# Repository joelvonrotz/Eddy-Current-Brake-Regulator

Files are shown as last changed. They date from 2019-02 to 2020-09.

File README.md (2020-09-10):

# Eddy Current Brake Regulator
This Repository is for the storage of all files and references used in the documentation.
Additionally the mechanical plans, KiCAD files, used for the PCB, and the Latex Project is included here.

# Geregelte Wirbelstrombremse
Dieses *Repository* beinhaltet alle verwendeten Informationen bezüglich der Maturaarbeit *Geregelte Wirbelstrombremse*. Alle mechanischen Pläne, Leiterplattendaten und das Latex-Projekt selber wird hier abgespeichert.

:warning: This is my very first Latex-project, so expect a lot of workarounds :warning:

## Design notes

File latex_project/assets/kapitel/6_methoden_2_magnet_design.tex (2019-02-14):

\subsection{Magnet Design}\label{cap:methoden_magnet_design}
Die Form des Magneten war abhängig von mehreren Faktoren. Einerseits musste der Magnet anhand der elektronischen Vorgaben angepasst werden, anderseits limitierte das Rad des Fitnesstrainers den Platz für den Magnet.

\input{assets/images/manget_uc.tex}

Im Normalfall besteht eine Magnetbremse aus einer Metall-Scheibe, welche eine gute Leitfähigkeit besitzt, und einem C-förmiger Magnet, welcher in der Öffnung die Scheibe platziert wird. Wenn der Platz ungenügend ist, kann eine zusätzliche eisenhaltige Scheibe hinzugefügt werden und der C-förmige Magnet durch einen U-förmigen Magnet ersetzt werden, wobei dieser nicht unten platziert wird, sondern seitlich der Scheibe (Siehe Abbildung \ref{fig:magnet_uc}). Dieser Aufbau erlaubt es, die zu bremsende Scheibe von der Seite an zu bremsen, anstatt von unten. Der Nachteil ist der Energieverlust zwischen den Luftspalten, welcher sich fast verdoppelt. 
\newpara
Da das Rad des Fitnesstrainers zu breit ist und daher den Platz für ein C-förmiger Magnet zu eng ist, wurde für ein U-förmiges Magnet entschieden. Im Anhang können die Pläne für die Eisen- und Aluminium-Platte und für das Magnet gefunden werden. Diese Pläne wurden in der CAD-Software \textit{Fusion 360} von Autodesk erstellt.
\newpara
Der Magnet wurde anhand der von W.R. Smythe geschriebenen Arbeit \textit{Eddy Current on a Rotating Disk}(\cite{current_on_a_rotating_disk}) erstellt. Diese Formel wurde von Empfehlung einer externen Person verwendet, da diese Person mit dieser Formel gearbeitet hatte. Von Smythes Arbeit wurde die Formel 22 für die Berechnung des Magneten verwendet (Siehe Formel \ref{equ:smythe_orignal}).

\begin{equation}
  \label{equ:smythe_orignal}
  M = \frac{\omega_{MAX}\cdot b \cdot \gamma \cdot \Phi^{2}\cdot c^{2}}{2\cdot\pi\cdot a^{2}}\cdot(1-\frac{A^{2}\cdot a^{2}}{(A^{2}-c^{2})^{2}})
\end{equation}
\begin{gather}
\shortintertext{\textbf{Begriffe:}}
\begin{tabularx}{0.9\textwidth}{ll}
  $\omega_{MAX}$	& maximale Kreisfrequenz\\
  $\Phi$          & Magnetischer Fluss \\
  $\gamma$	      & Elektronische Leitfähigkeit der Spule am Magnet\\
  $a$             & Radius der Magnetpoolfläche welche auf die Scheibe gerichtet ist\\
  $c$             & Radius der Magnetposition von dem Mittelpunkt der Scheibe ausgerichtet\\
  $b$             & Dicke der Scheibe\\
  $A$             & Radius der Scheibe (nur für diese Formel)\\
  $M$             & Drehmoment
\end{tabularx}\nonumber
\end{gather}

Die maximale Kreisfrequenz wurde anhand einer Drehzahlmessung mit dem Messgerät \textit{Braun gmbh MOVIPORT C118} und mit einem menschlichen Versuchstier ermittelt. Durch starkes Antreten der Pedale mit dem Messgerät konnte die maximale Drehzahl ermittelt werden. Wird die Formel der Kreisfrequenz (Siehe Formel \ref{equ:rotation_max}) in die Formel (Formel \ref{equ:smythe_orignal}) eingesetzt, kann die Kreisfrequenz durch die Drehzahl ersetzt werden (Siehe Formel \ref{equ:smythe_rotation_included}).

\begin{equation}
  \label{equ:rotation_max}
  \omega_{MAX}=2\cdot\pi n_{MAX}
\end{equation}
\begin{gather}
\shortintertext{\textbf{Begriffe:}}
\begin{tabularx}{0.9\textwidth}{ll}
  $n_{MAX}$	& maximale Drehzahl
\end{tabularx}\nonumber
\end{gather}
(\cite[S.193]{kuchling2014taschenbuch})
\newpara
\begin{equation}
  \label{equ:smythe_rotation_included}
  M = \frac{\cancel{2\cdot\pi}\cdot n_{MAX}\cdot b \cdot \gamma \cdot \Phi^{2}\cdot c^{2}}{\cancel{2\cdot\pi}\cdot a^{2}}\cdot(1-\frac{A^{2}\cdot a^{2}}{(A^{2}-c^{2})^{2}})
\end{equation}

Die gesamte Form des Magneten wird anhand des magnetischen Flusses berechnet, da in der Formel des Flusses (Siehe Formel \ref{equ:magnetischer_fluss}) der magnetische Widerstand, welche abhängig von der Form des Magneten ist, und die magnetische Durchflutung (Siehe Formel \ref{equ:magnetische_durchflutung}), welche von der Stromstärke und der Anzahl Wicklungswindungen am Magnet abhängig ist, eingesetzt wird. Der magnetische Widerstand besteht aus mehreren Teilwiderstände, welche allen Teilen des Magneten und der Luftspalte entsprechen (Siehe Formel \ref{equ:magnetischer_widerstand} \& \ref{equ:magnetischer_serie_widerstand}).

\begin{equation}
  \label{equ:magnetischer_fluss}
  \Phi = \frac{\Theta}{R_m}
\end{equation}
\begin{gather}
\shortintertext{\textbf{Begriffe:}}
\begin{tabularx}{0.9\textwidth}{ll}
  $\Theta$	 &  magnetische Durchflutung\\
  $\Phi$	 &  magnetischer Fluss\\
  $Rm$ &  magnetischer Widerstand
\end{tabularx}\nonumber
\end{gather}
(\cite{schulmaterial_magnetismus})
\newpage
\begin{equation}
  \label{equ:magnetische_durchflutung}
  \Theta = N\cdot I
\end{equation}
\begin{gather}
\shortintertext{\textbf{Begriffe:}}
\begin{tabularx}{0.9\textwidth}{ll}
  $N$	 &  Anzahl Windungen der Wicklung\\
  $I$	 &  elektrische Stromstärke
\end{tabularx}\nonumber
\end{gather}
(\cite{schulmaterial_magnetismus})
\newpara
\begin{figure}[ht]
  \begin{center}
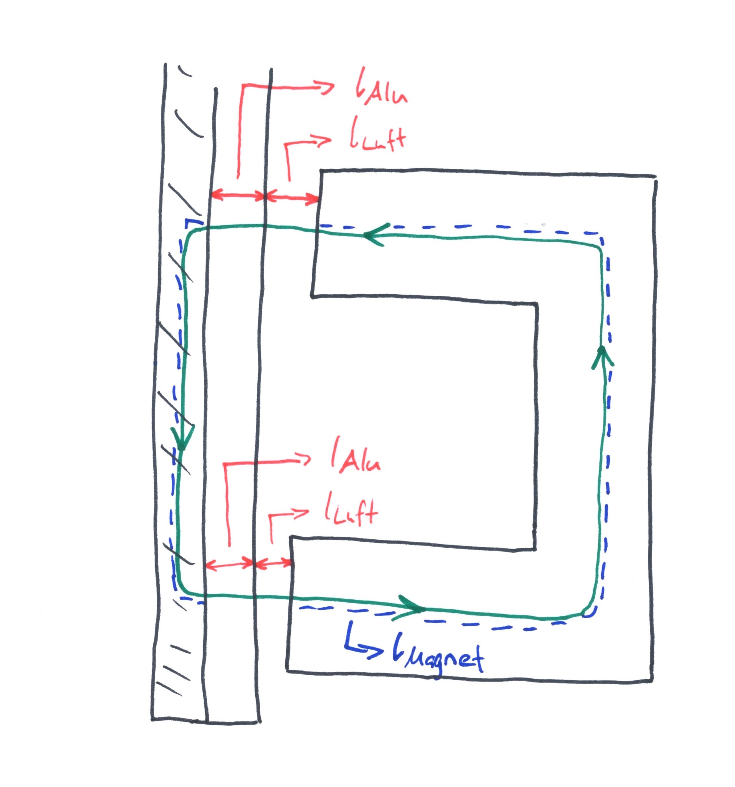
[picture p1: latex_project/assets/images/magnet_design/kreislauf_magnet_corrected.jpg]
    
  \end{center}
  \vspace{-3ex}
  \caption{Magnetkreis bei Magnet und Scheibe}
  \label{fig:magnet_kreisllaenge}
\end{figure}
\newpage
\begin{equation}
  \label{equ:magnetischer_widerstand}
  R_m=\frac{l}{\mu_0 \cdot \mu_r \cdot A}
\end{equation}
\begin{gather}
\shortintertext{\textbf{Begriffe:}}
\begin{tabularx}{0.9\textwidth}{ll}
  $\mu_0$  & magnetische Feldkonstante = 1.257E-06	Vs/Am\\
  $\mu_r$  & Permeabilitätszahl (1 $\equalhat$ Vakuum, $\gg$ 1 $\equalhat$ ferromagnetisch)\\
  $A$	  & Querschnittsfläche des Elements\\
  $R_m$  & Magnetischer Widerstand\\
  $l$	  & Länge des magnetischen Kreises (Siehe Abbildung \ref{fig:magnet_kreisllaenge})
\end{tabularx}\nonumber
\end{gather}
(\cite{schulmaterial_magnetismus})
\newpara
Mit dem magnetischen Widerstand (Siehe Formel \ref{equ:magnetischer_widerstand}) wird in Kombination mit der magnetischen Durchflutung die Magnetstärke (magnetischer Fluss) berechnet. Wird ein starkes Magnet benötigt, wird je nach Möglichkeit entweder die Durchflutung angepasst oder der magnetische Widerstand durch Verkleinerung des Luftspaltes.
\newpara
Der Luftspalt reduziert die magnetische Flussdichte, was den Magneten davon abhält, gesättigt zu werden. Ist ein Magnet gesättigt, wird überflüssige Energie in Wärme umgewandelt. Der Effekt des Luftspalts ist wegen dem magnetischen Widerstand des Vakuums. Die Permeabilitätszahl vom Vakuum ist gleich $1$ und entspricht daher der magnetischen Feldkonstante ($\mu_0 \cdot 1 = \mu_0$). Bereits bei einer Querschnittsfläche von $1m^2$ und einem Luftspalt von $1m$ beträgt der magnetische Widerstand $\frac{1m}{1\cdot 1.257\cdot 10^{-6}\frac{N}{A^2}\cdot 1m^2}=795'798\frac{A}{Vs}$. Bei einem Eisenstück mit einer Permeabilitätszahl von $10'000$ würde der magnetische Widerstand $\frac{1m}{10'000\cdot 1.257\cdot 10^{-6}\frac{N}{A^2}\cdot 1m^2}=79,58\frac{A}{Vs}$ entsprechen, 10'000 kleiner als der Widerstand des Luftspalts. Der Nachteil des Luftspalts ist die Schwächung der Magnetstärke, was zu einer schwächeren Bremse führt.
\newpara
Bei der Wirbelstrombremse ist es wichtig, ein starkes Magnet zu haben. Das bedeutet, dass einen kleinen magnetischen Widerstand benötigt wird.
\newpara

\begin{equation}
  \label{equ:magnetischer_serie_widerstand}
  R_{mGES}=R_{m Luft}+R_{m Alu}+R_{m Magnet}
\end{equation}
\begin{gather}
\shortintertext{\textbf{Begriffe:}}
\begin{tabularx}{0.9\textwidth}{ll}
  $R_{mGES}$  & magnetische Gesamtwiderstand\\
  $R_{m Luft}$  & mag. Widerstand der Luftspalte\\
  $R_{m Alu}$  & mag. Widerstand der Aluminiumscheibe\\
  $R_{m Magnet}$  & mag. Widerstand des Magneten\\
\end{tabularx}\nonumber
\end{gather}
(\cite{schulmaterial_magnetismus})
\newpara
Der gesamte magnetische Widerstand ist abhängig von der Dicke der Aluminiumscheibe, der Dicke des Luftspalts und die magnetischen Kreislänge des Magneten (Siehe Formel \ref{equ:magnetischer_serie_widerstand}). Abbildung \ref{fig:magnet_design_u_magnet_luftspalt} zeigt den Nachteil eines seitlichen Aufbaus im Vergleich eines C-förmigen Magneten (Siehe Abbildung \ref{fig:magnet_design_c_magnet_luftspalt} folgende Seite).  
\begin{figure}[ht]
\begin{center}
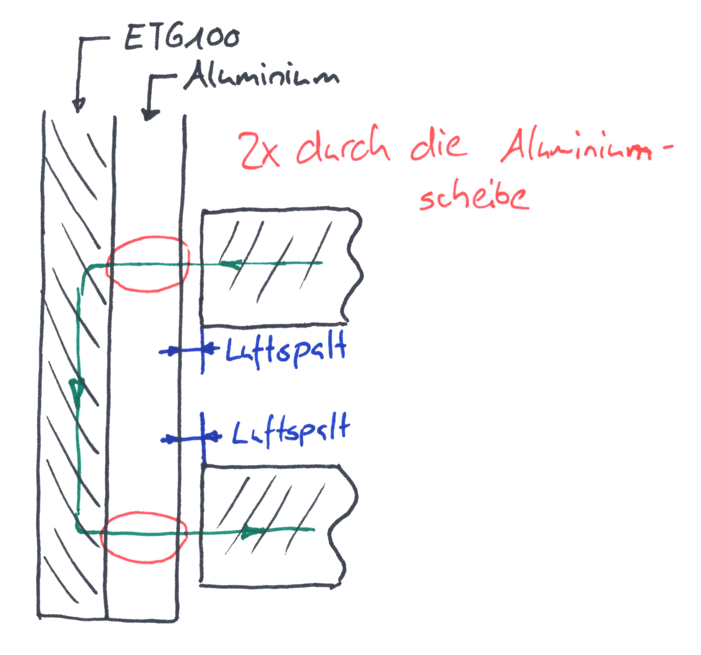
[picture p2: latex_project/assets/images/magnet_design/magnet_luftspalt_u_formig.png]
  
\end{center}
\vspace{-3ex}
\caption{Luftspalt eines U-förmigen Magnets}
\label{fig:magnet_design_u_magnet_luftspalt}
\end{figure}

\begin{figure}[ht]
\begin{center}
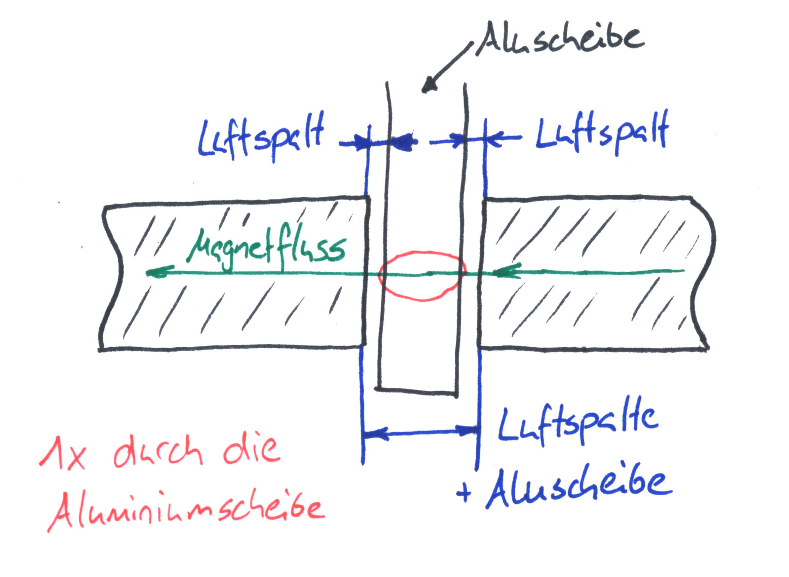
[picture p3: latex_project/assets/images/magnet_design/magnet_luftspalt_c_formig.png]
  
\end{center}
\vspace{-3ex}
\caption{Luftspalt eines C-förmigen Magnets}
\label{fig:magnet_design_c_magnet_luftspalt}
\end{figure}

Der Luftspalt kann gleich behalten werden, aber die Kreislänge der Aluminiumscheibe verdoppelt sich, was zu einem doppelten Aluminiumwiderstand führt (Siehe Formel \ref{equ:magnetischer_widerstand_alueinfluss}). Da Aluminium dem Vakuum sehr nahe kommt, hat dies einen grossen Einfluss auf die Magnetstärke.

\begin{equation}
  \label{equ:magnetischer_widerstand_alueinfluss}
  R_m=R_{m Luft}+2 \cdot R_{m Alu}+R_{m Magnet}
\end{equation}
\newpara
Das Drehmoment M in der Formel \ref{equ:smythe_rotation_included} wird durch das Trägheitsdrehmoment ersetzt (Siehe Formel \ref{equ:Drehmoment_tragheit}), da die Bremse abhängig von der zu bremsenden Scheibe ist.

\begin{equation}
  \label{equ:Drehmoment_tragheit}
  M=J\cdot\alpha
\end{equation}
\begin{gather}
\shortintertext{\textbf{Begriffe:}}
\begin{tabularx}{0.9\textwidth}{ll}
  $M$  & Drehmoment\\
  $J$  & Trägheitmoment\\
  $\alpha$ & Winkelbeschleunigung
\end{tabularx}\nonumber
\end{gather}
(\cite[S.127]{kuchling2014taschenbuch})
\newpara
Das Trägheitsmoment gibt die Beeinflussung der Masse von der Scheibe auf die Bremse an (Siehe Formel \ref{equ:tragheitsmoment}). Die Winkelgeschwindigkeit gibt die zeitliche Änderung der Winkelgeschwindigkeit innerhalb von zwei Zeitpunkten an (Siehe Formel \ref{equ:winkelbeschleunigung}).

\begin{equation}
  \label{equ:tragheitsmoment}
  J=m\cdot r^2
\end{equation}
\begin{gather}
\shortintertext{\textbf{Begriffe:}}
\begin{tabularx}{0.9\textwidth}{ll}
  $J$  & Trägheitsmoment\\
  $m$  & Masse der Scheibe\\
  $r$ & Radius der Scheibe
\end{tabularx}\nonumber
\end{gather}
(\cite[S.131]{kuchling2014taschenbuch})
\newpara
\begin{equation}
  \label{equ:winkelbeschleunigung}
  \alpha=\frac{\Delta\omega}{\Delta t}
\end{equation}
\begin{gather}
\shortintertext{\textbf{Begriffe:}}
\begin{tabularx}{0.9\textwidth}{ll}
  $\Delta\omega$  & Kreisfrequenzänderung während der Zeit $\Delta t$\\
  $\Delta t$  & Zeit während zwei Zeitpunkten \\
\end{tabularx}\nonumber
\end{gather}
(\cite[S.88]{kuchling2014taschenbuch})
\newpara
Die Kreisfrequenzänderung und die Zeitdifferenz sind bei der Berechnung Annahmen (der Wert wurde von der Gruppe vorgegeben).
\newpara
Nun wurde die Formel \ref{equ:tragheitsmoment} und die Formel \ref{equ:winkelbeschleunigung} in die Formel \ref{equ:Drehmoment_tragheit} eingesetzt, was zu einer neuen Formel führt (Formel \ref{equ:tragheitsmoment_kombiniert}). Die Dimensionierung basiert nun auf dem \textit{Trial-and-Error} Prinzip. Mit unterschiedlichen Dimensionen wird die Formel (Formel \ref{equ:smythe_rotation_included}) verwendet, bis anhand eines nutzbaren Resultats die Dimensionen des Magnets ermittelt werden konnte. 
\newpara
\begin{equation}
  \label{equ:tragheitsmoment_kombiniert}
  M=\frac{m\cdot r^2\cdot\Delta\omega}{\Delta t}
\end{equation}
\newpara
Folgende Angaben wurde für den aktuellen Magneten verwendet:
\newpara
\begin{tabularx}{0.9\textwidth}{lll}
$\mu_R$	       & $3000$		&Annahme, da kein definitiver Wert existiert\\
$N$	           & $300$		\\
$I$	           & $2 A$\\
$l_{LUFT}$	   & $8 mm$\\
$l_{Fe}$ 	     & $1.05 mm$\\
$a$	           & $0.015 m$\\
$b$	           & $0.003 m$\\
$c$	           & $0.1 m$\\
$A$	           & $0.15 m$\\
$n_{MAX}$	     & $25 s^{-1}$	\\
$\Delta\omega$ & $5 s^{-1}$	  &	Gewünschte Abbremsung innerhalb $\Delta t$\\
$\Delta t$	   & $5 s$        &	Zeit für $\Delta\omega$\\
$\alpha$	     & $1 rad\cdot s^{-2}$&	Winkelbeschleunigung von $\Delta t$ und $\Delta\omega$\\
$m_{RAD}$	     & $5.747 kg$	  & Gewicht des Rades\\
$\Phi$	       & $76.43\cdot 10^{-6} Vs$\\
$\gamma$	     & $6.21\cdot 10^{6} Sm^{-1}$
\end{tabularx}\nonumber
\newpara
daraus ergab sich:
\newpara
\begin{tabularx}{0.9\textwidth}{lll}
  $M_{MAG}$	   & $0.0186 Nm$		& Drehmoment der Bremse\\
  $M_{MASS}$   & $0.00647 Nm$		& Trägheit des Rades\\
\end{tabularx}\nonumber
\newpara
Anhand dieser Resultate sollte der Magnet stärker sein als die Massenträgheit der Scheibe. Was sich aber bei den Messungen herausstellte, stimmte dieser Wert nicht überein mit den Resultaten. Die Begründung, warum diese Resultate nicht stimmen, wird im Kapitel \ref{cap:diskussion} erläutert.
\newpara
\begin{tcolorbox}
  Hier geschahen der erste und zweite Fehler: 1) das Trägheitsdrehmoment (Formel \ref{equ:Drehmoment_tragheit}) wurde nicht mit der Formel von Smythe (Formel \ref{equ:smythe_rotation_included}) kombiniert, sondern die beiden Drehmomente wurden verglichen, was zu einem eher ungenauen Magneten führte. 
  \newpara
  2) Der zweite Fehler ist die Fehlberechnung der Dimensionen. Anstatt die Formel (Formel \ref{equ:smythe_rotation_included}) korrekt zu verwenden wurde stattdessen mit der folgenden Formel (Formel \ref{equ:wrong_calculation}) gerechnet. Die Winkelfrequenz-Formel wurde nicht korrekt eingesetzt und gekürzt, was zu einem falschen Resultat führte.

  \begin{equation}
    \label{equ:wrong_calculation}
    M=\frac{n_{MAX}\cdot b\cdot\gamma\cdot\Phi^2\cdot c^2}{2\cdot\pi\cdot a^2}\cdot(1-\frac{A^{2}\cdot a^{2}}{(A^{2}-c^{2})^{2}})
  \end{equation}
  \newpara
  Im Kapitel \ref{cap:diskussion} wird die vollständige Formel aufgeführt.
\end{tcolorbox}

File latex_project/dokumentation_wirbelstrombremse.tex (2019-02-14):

%!TEX TS-program = xelatex
%!TEX encoding = UTF-8 Unicode

\documentclass[12pt]{article} % A4 paper size, default 11pt font size and oneside for equal margins
\usepackage[bottom=2.54cm, left=2.54cm, right=2.54cm, top=2.54cm]{geometry}
\usepackage[english,german]{babel}
\usepackage[toc,numberedsection]{glossaries}
\usepackage[style=alphabetic, citestyle=authoryear,date=iso, urldate=iso]{biblatex}
\usepackage{titlesec}
\usepackage[x11names]{xcolor}
\usepackage{tcolorbox}
\usepackage{scalerel,stackengine,amsmath}
\usepackage{textcomp}
\usepackage[T1]{fontenc}
\usepackage{tikz}
\usepackage{pgfplots}
\usepackage{siunitx}
\usepackage{mathtools}
\usepackage{cancel}
\usepackage{qrcode}
\usepackage{tabularx}
\PassOptionsToPackage{hyphens}{url}
\usepackage{hyperref}
\usepackage{dirtytalk}
\usepackage{float}

\batchmode

\renewcommand*{\nameyeardelim}{\addcomma\space}
\usetikzlibrary{positioning,fit,calc,arrows.meta,arrows}
\usepgfplotslibrary{units}
\newcommand\equalhat{\mathrel{\stackon[1.5pt]{=}{\stretchto{%
    \scalerel*[\widthof{=}]{\wedge}{\rule{1ex}{3ex}}}{0.5ex}}}}

\tikzset{
  labelbox/.style={draw,thick,text width=2.5cm,minimum height=1cm,align=center},
  round/.style={circle,draw,thin, minimum size=5mm},
  emptynode/.style={draw=none},
  arrow_right/.style={-{Latex[length=2mm]}},
  spot/.style={draw,shape=circle,fill=black,inner sep=1.5pt, minimum size = 0.5mm}
}

\pgfplotsset{
  compat=1.16,
  axis_regulator_style/.style={
    width=8.8cm,
    axis x line=center,
    axis y line=left,
    xlabel style={right = 0cm and 0.1cm},
    ylabel style={above left},
    legend cell align={left}
  },
  axis_results_style/.style={
    width=8.8cm,
    axis x line=bottom,
    axis y line=left,
    legend cell align={left}
  },
  line_black/.style={
    color=black!70,
    line width= 1pt
  },
  line_blue/.style={
    color=blue!70,
    line width= 1pt
  },
  line_red/.style={
    color=red!70,
    line width= 1pt
  }
}

\newcommand{\newpara}
{
  \vskip 0.5cm
}
\raggedbottom

\newlength\tindent
\setlength{\tindent}{\parindent}
\setlength{\parindent}{0pt}
\renewcommand{\indent}{\hspace*{\tindent}}

% \usepackage{newtxtext}
% \usepackage{amsmath}
% \usepackage[mathrm=sym]{unicode-math}
% \setmathfont{Fira Math}

%----------------------------------------------------------------------------------------
%	TITLE PAGE
%----------------------------------------------------------------------------------------

\makeglossaries
\loadglsentries{assets/glossar.tex}
\bibliography{literature_and_stuff}

\begin{document} 
\input{assets/titlepage.tex}
\tableofcontents
\vskip 2cm

\input{assets/kapitel/1_vorwort.tex}

\input{assets/kapitel/2_abstract.tex}
\newpage

\input{assets/kapitel/3_einleitung.tex}
\newpage
\section{Einlesung}\label{cap:einlesung}
\input{assets/kapitel/4_einlesung_1_magnetismus.tex}
\input{assets/kapitel/4_einlesung_2_physik.tex}
\input{assets/kapitel/4_einlesung_3_regler.tex}
\newpage
\section{Material}\label{cap:material}
\input{assets/kapitel/5_material_1_mechanik.tex}
\input{assets/kapitel/5_material_2_magnet.tex}
\input{assets/kapitel/5_material_3_elektronik.tex}

\section{Methoden}\label{cap:methoden}
\input{assets/kapitel/6_methoden_1_planung.tex}
\newpage
\input{assets/kapitel/6_methoden_2_magnet_design.tex}
\input{assets/kapitel/6_methoden_3_leiterplatten.tex}
\newpage
\input{assets/kapitel/6_methoden_4_aufbau.tex}
\input{assets/kapitel/6_methoden_5_drehzahl.tex}
\input{assets/kapitel/6_methoden_6_magnetbremsung.tex}
\newpage
\input{assets/kapitel/6_methoden_7_radanpassung.tex}
\newpage
\input{assets/kapitel/6_methoden_8_datenauswertung.tex}
\newpage
\input{assets/kapitel/6_methoden_9_magnet_control.tex}
\newpage
\section{Ergebnisse}\label{cap:ergebnisse}
\input{assets/kapitel/7_ergebnisse_1_drehzahlmessung.tex}
\newpage
\input{assets/kapitel/7_ergebnisse_2_magnetabbremsung.tex}
\newpage
\section{Diskussionen} \label{cap:diskussion}
\input{assets/kapitel/8_diskussion_1_drehzahlmessung.tex}
\input{assets/kapitel/8_diskussion_2_magnetabbremsung.tex}
\newpage
\input{assets/kapitel/8_diskussion_3_nichterreichung.tex}
\input{assets/kapitel/8_diskussion_4_schlussfolgerung.tex}

\section{Schlusswort} \label{cap:schlusswort}
\input{assets/kapitel/9_schlusswort.tex}
\newpage

\input{assets/kapitel/10_abbildungsverzeichnis.tex}
\newpage

\input{assets/kapitel/11_glossar.tex}
\newpage

\input{assets/kapitel/12_literaturverzeichnis.tex}
\newpage

\section{Anhang}
\input{assets/kapitel/13_anhang.tex}

% https://www.latextemplates.com/template/formal-book-title-page - template

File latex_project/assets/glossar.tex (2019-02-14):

\newglossaryentry{glos:frequenz}
{
  name={Frequenz},
  description={Anzahl der Schwingungen im Verhältnis zu der dafür benötigten Zeit}
}

\newglossaryentry{glos:kinetische_energie}
{
  name={Kinetische Energie},
  description={Das ist die Energie, welche in einem sich bewegenden Körper gespeichert ist. Wird auch als Energie der Bewegung bezeichnet.}
}

\newglossaryentry{glos:induktion}
{
  name={Induktion},
  description={Zeitliche Änderung des magnetischen Flusses, die durch die Bewegung eines Leiters im Magnetfeld Erzielt wird. Im Leiter entsteht eine elektrische Spannung.}
}

\newglossaryentry{glos:wirbelstrom}
{
  name={Wirbelstrom},
  description={Bewegt sich ein elektrisch leitender Körper in einem Magnetfeld, wird in dem Teil, der sich gerade durch das Magnetfeld bewegt eine Spannung induziert. Das führt zu einer Spannungsdifferenz im Körper. Diese wird mit Wirbelströmen ausgeglichen.}
}

\newglossaryentry{glos:magnetfeld}
{
  name={Magnetfeld},
  description={Raum, in dem ein Magnet Kraft ausübt.}
}

\newglossaryentry{glos:ferromagnetisch}
{
  name={Ferromagnetisch},
  description={Stoffe, die von Magneten angezogen werden.}
}

\newglossaryentry{glos:elektronen}
{
  name={Elektronen},
  description={Negativ geladenes Teilchen n der Atomhülle.}
}

\newglossaryentry{glos:magnetischer_fluss}
{
  name={Magnetischer Fluss},
  description={Die Gesamtzahl aller Magnetischen Feldlinien in einem Magneten.}
}

\newglossaryentry{glos:c_schiene}
{
  name={C-Schiene},
  description={C-förmiges Metallstück, welches für Befestigungen von Elektronik dient.}
}

\newglossaryentry{glos:etg_100}
{
  name={ETG-100},
  description={Metall mit Eiseninhalt.}
}

\newglossaryentry{glos:mcu}
{
  name={Mikrocontroller},
  description={Ein Baustein, welcher aus Halbleitern besteht. Können meistens in kleinen simplen Geräten aufgefunden werden, wie zum Beispiel in einer Fernbedienung.}
}

\newglossaryentry{glos:fpu}
{
  name={FPU},
  description={Steht für Floating Point Unit und wird für Berechnungen von Kommazahlen verwendet.}
}

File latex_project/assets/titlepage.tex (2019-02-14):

\begin{titlepage} % Suppresses headers and footers on the title page

	\centering % Centre everything on the title page
  \vspace*{10mm}
  {\LARGE GEREGELTE} % Title
  \newpara
  {\LARGE WIRBELSTROMBREMSE}
  \vskip 10mm
  \input{assets/images/aufbau.tex}

  {Verfasser}

	{\Large Joel von Rotz \\ Stefan Ruckli \\ \vspace{0.25\baselineskip} Filip Estermann} % Editor list
  \vskip 1cm
    Betreuungslehrperson

    {\large Antonio Russo}
  \vskip 1cm
	\textit{BBZB Luzern} % Editor affiliation
  Februar 2019 % Publication year
	{IDPA-Nr. 1094} % Publisher

\end{titlepage}

%----------------------------------------------------------------------------------------
\author{Joel von Rotz\\Stefan Ruckli\\Filip Estermann}
\date{Februar 2019}

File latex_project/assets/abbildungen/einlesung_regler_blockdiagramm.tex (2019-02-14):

\begin{figure}[ht]
  \begin{center}
    \begin{tikzpicture}
      \node[emptynode]    (soll)                                {};
      \node[round]        (diff)        [right=1cm of soll]     {};
      \node[labelbox]     (regl)        [right=1cm of diff]     {Regler};
      \node[labelbox]     (akto)        [right=1cm of regl]     {Aktor};
      \node[labelbox]     (sens)        [below=1cm of akto]     {Sensor};
      \node[labelbox]     (stre)        [right=1cm of akto]     {Regelstrecke};
      \node[emptynode]    (gone)        [right=2cm of stre]     {};
      \node[emptynode]    (erro)        [above=1cm of stre]     {z};
      \node[emptynode]    (minus_diff)  [below right = -1mm and -1mm of diff] {$-$};
      %\node[emptynode]    (plus_diff)   [above left  = -1mm and -1mm of diff] {$+$};
      \node[spot]         (midl)        [right=1cm of stre]     {};

      \draw [arrow_right] (soll)      -- node[above left = 0cm and 1mm]   {$w$} (diff);
      \draw [arrow_right] (diff)      -- node[above left = 0cm and -1mm]  {$e$} (regl);
      \draw [arrow_right] (regl)      -- node[above]                      {$m$} (akto);
      \draw [arrow_right] (akto)      -- node[above]                      {$y$} (stre);
      \draw [-]           (stre)      -- node[above left]                 {$x$} (gone);
      \draw [arrow_right] (midl.center) |-                                      (sens.east);
      \draw [arrow_right] (sens.west) -| node[above left  = 1cm and 0cm]  {$r$} (diff.south);
      \draw [arrow_right] (erro)      --                                            (stre);
    \end{tikzpicture}
  \end{center}
  \vspace{-3ex}
  \caption{Regler Blockdiagramm}
  \label{fig:regulator_block}
\end{figure}

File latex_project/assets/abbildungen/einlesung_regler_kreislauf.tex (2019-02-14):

\begin{figure}[ht]
  \begin{center}
    \begin{tikzpicture}
      \node[labelbox]     (mess)                                          {Messen};
      \node[labelbox]     (verg)  [below right= 3cm and 0.5cm of mess]    {Vergleichen};
      \node[labelbox]     (stel)  [below left = 3cm and 0.5cm of mess]    {Stellen};

      \node[emptynode]    (nod0)  [below right= 0.2cm and 0.2cm of mess]  {};
      \node[emptynode]    (nod1)  [above      = 0.2cm of verg]            {};
      \node[emptynode]    (nod2)  [      left = 0.2cm of verg]            {};
      \node[emptynode]    (nod3)  [      right= 0.2cm of stel]            {};
      \node[emptynode]    (nod4)  [above      = 0.2cm of stel]            {};
      \node[emptynode]    (nod5)  [below left = 0.2cm and 0.2cm of mess]  {};

      \draw [arrow_right] (nod0) -- (nod1);
      \draw [arrow_right] (nod2) -- (nod3);
      \draw [arrow_right] (nod4) -- (nod5);

    \end{tikzpicture}
  \end{center}
  \vspace{-3ex}
  \caption{Regler Blockdiagramm}
  \label{fig:regulator_circulation}
\end{figure}

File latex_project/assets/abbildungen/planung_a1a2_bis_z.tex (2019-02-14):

\begin{figure}[ht]
    \begin{center}
      \begin{tikzpicture}
        \node[emptynode]     (a1)                                        {$A_1$};
        \node[emptynode]     (a2)   [below= 2cm of a1]                     {$A_2$};
        \node[emptynode]     (z)    [below right= 0.9cm and 5cm of a1]                     {Z};
        \node[emptynode]     (e1)   [right= 2cm of a1]                                  {};
        \node[emptynode]     (e2)   [right= 2cm of a2]                     {};
        \node[emptynode]     (e3)   [below right= 1cm and 3cm of a1]                     {};
  
        \draw [-] (a1) -- (e1.center);
        \draw [-] (a2) -- (e2.center);
        \draw [-] (e2.center) -- (e3.center);
        \draw [-] (e1.center) -- (e3.center);
        \draw [arrow_right] (e3.center) -- (z);
      \end{tikzpicture}
    \end{center}
    \vspace{-3ex}
    \caption{Parallele Vorgehensweise}
    \label{fig:planung_a1a2_bis_z}
  \end{figure}

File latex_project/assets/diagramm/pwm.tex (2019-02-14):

\begin{figure}[h]
  \begin{center}
    \begin{tikzpicture}
      \begin{axis}[
        axis_regulator_style,
               %title         = P-Regler mit konstanter Abweichung,
               ylabel         = {Spannung},
               y unit         = {V},
        ylabel near ticks, 
        yticklabel pos        = left,
        minor      grid style = {dashed,gray},
                   ymax       = 2,
                   ymin       = 0,
                   xmax       = 20,
                   xlabel     = {t},
                   xticklabels    = {,,},
        legend     style      = {draw=none}
      ]
      
        \addplot[line_red] table[x=time,y=value,col sep=comma,mark=none]{assets/diagramm/pwm.csv};
        \addlegendentry{PWM-Verlauf}
      \end{axis}
      \draw[<->](0.37,2) -- node[above]{Pause} (2.88,2);
      \draw[<->](2.90,2) -- node[right =0.3cm]{Impuls} (3.60,2);
      \draw[-](0.37,3) -- (0.37,4);
      \draw[-](3.62,3) -- (3.62,4);
      \draw[<->](0.37,3.8) -- node[above]{Periode} (3.62,3.8);
    \end{tikzpicture}
  \end{center}
  \vspace{-3ex}
  
  \caption{PWM Darstellung}
  \label{fig:plot_pwm}
\end{figure}

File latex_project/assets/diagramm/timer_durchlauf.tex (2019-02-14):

\begin{figure}[h]
  \begin{center}
    \begin{tikzpicture}
      \begin{axis}[
        axis_regulator_style,
               %title         = P-Regler mit konstanter Abweichung,
               yticklabels    = {,,},
               xticklabels    = {,,},
        ylabel near ticks, 
        yticklabel pos        = left,
        minor      grid style = {dashed,gray},
                   ymax       = 10,
                   ymin       = 0,
                   xmax       = 20,
                   xlabel     = {t},
        legend     style      = {draw=none}
      ]
        \addplot[line_blue] table[x=time2,y=value2,col sep=comma,mark=none]{assets/diagramm/timer_durchlauf.csv};       
        \addlegendentry{Magnetschalter}
      
        \addplot[line_red] table[x=time,y=value,col sep=comma,mark=none]{assets/diagramm/timer_durchlauf.csv};    
        \addlegendentry{Timer}
      \end{axis}
      \draw[<->](0,2.7) -- node[above]{Zeit für eine Umdrehung} (5.78,2.7);
      \draw[-,black!70,thick](5.78,0.6) -- (5.78,3.6);
    \end{tikzpicture}
  \end{center}
  \vspace{-3ex}
  
  \caption{Eine Radumdrehung}
  \label{fig:plot_timer_magnetschalter_impuls}
\end{figure}

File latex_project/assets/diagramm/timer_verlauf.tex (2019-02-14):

\begin{figure}[h]
  \begin{center}
    \begin{tikzpicture}
      \begin{axis}[
        axis_regulator_style,
               %title         = P-Regler mit konstanter Abweichung,
               ylabel         = {Zählerstand},
               xticklabels    = {,,},
        ylabel near ticks, 
        yticklabel pos        = left,
        minor      grid style = {dashed,gray},
                   ymax       = 23,
                   ymin       = 0,
                   xmax       = 20,
                   xlabel     = {t},
        legend     style      = {draw=none}
      ]
      
        \addplot[line_red] table[x=time,y=value,col sep=comma,mark=none]{assets/diagramm/timer_verlauf.csv}; 
        \addlegendentry{Timer}
      \end{axis}
      \draw[<->](2.90,2.8) -- node[above =0.3cm,font = {\fontsize{8 pt}{16 pt}\selectfont}]{Zeit für ein Inkrement} (3.25,2.8);
      \draw[-](3.25,2.5) -- (3.25,3);
      \draw[-](2.90,2.2) -- (2.90,3);
      \draw[-](5.77,4) -- (5.77,5);
      \draw[<->](0,4.8) -- node[above,font = {\fontsize{8 pt}{16 pt}\selectfont}]{Zeit für ein Interval} (5.77,4.8);
    \end{tikzpicture}
  \end{center}
  \vspace{-3ex}
  
  \caption{Intervall Durchgang des Timers}
  \label{fig:plot_timer_verlauf}
\end{figure}

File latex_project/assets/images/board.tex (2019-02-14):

\begin{figure}[ht]
    \begin{center}
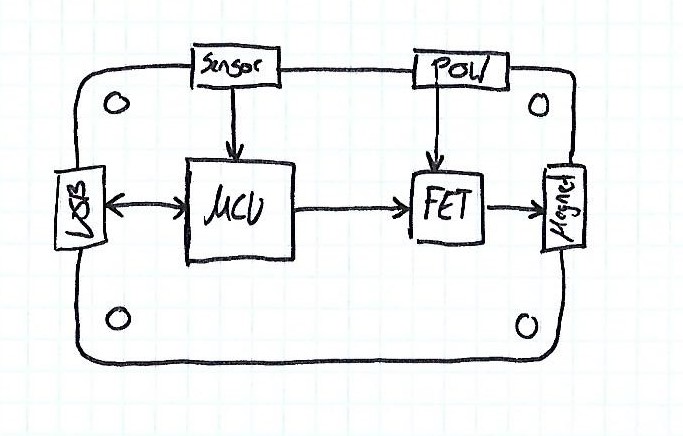
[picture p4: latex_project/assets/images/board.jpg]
      
    \end{center}
    \vspace{-3ex}
    \caption{Skizze des Leiterplattenlayouts}
    \label{fig:board}
  \end{figure}

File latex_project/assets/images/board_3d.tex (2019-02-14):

\begin{figure}[ht]
    \begin{center}
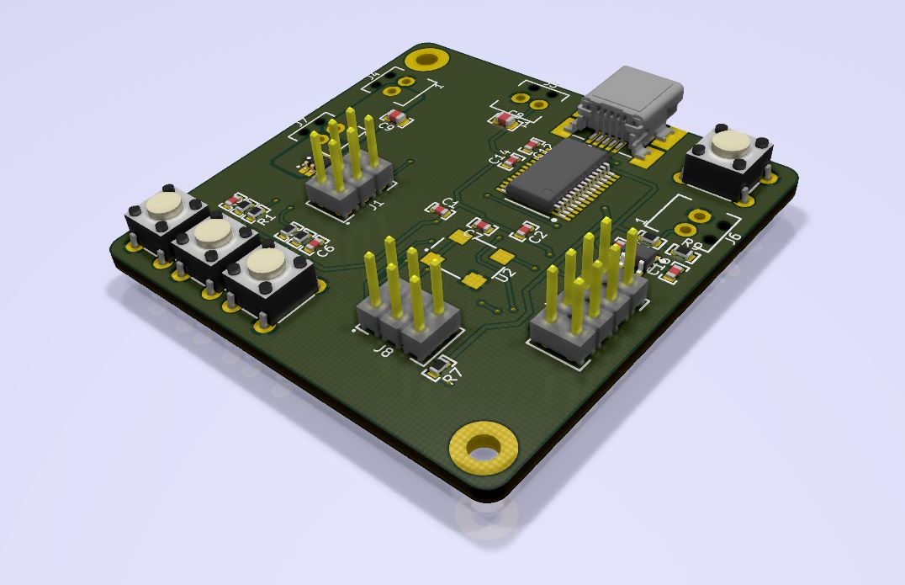
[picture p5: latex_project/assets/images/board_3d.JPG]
      
    \end{center}
    \vspace{-3ex}
    \caption{3D Model der fertigen Leiterplatte}
    \label{fig:3d_board}
  \end{figure}

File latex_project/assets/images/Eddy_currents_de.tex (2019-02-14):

\begin{figure}[ht]
    \begin{center}
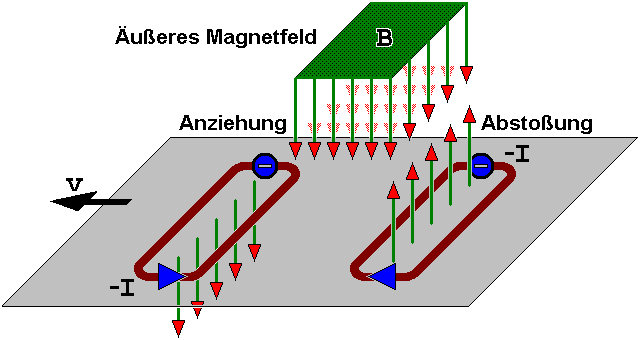
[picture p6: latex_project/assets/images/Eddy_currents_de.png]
      
    \end{center}
    \vspace{-3ex}
    \caption[Wirbelstrombremse auf einer Metallplatte]{\centering{Wirbelstrombremse auf einer Metallplatte. Heruntergeladen von \texttt{https://de.wikipedia.org/wiki/Wirbelstrombremse}}}
    \label{fig:eddy_current}
  \end{figure}

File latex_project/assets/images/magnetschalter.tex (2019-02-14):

\begin{figure}[ht]
    \begin{center}
      
    \end{center}
    \vspace{-3ex}
    \caption{Bild des Magnetschalter}
    \label{fig:magnetschalter}
  \end{figure}

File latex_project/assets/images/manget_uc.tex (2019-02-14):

\begin{figure}[ht]
    \begin{center}
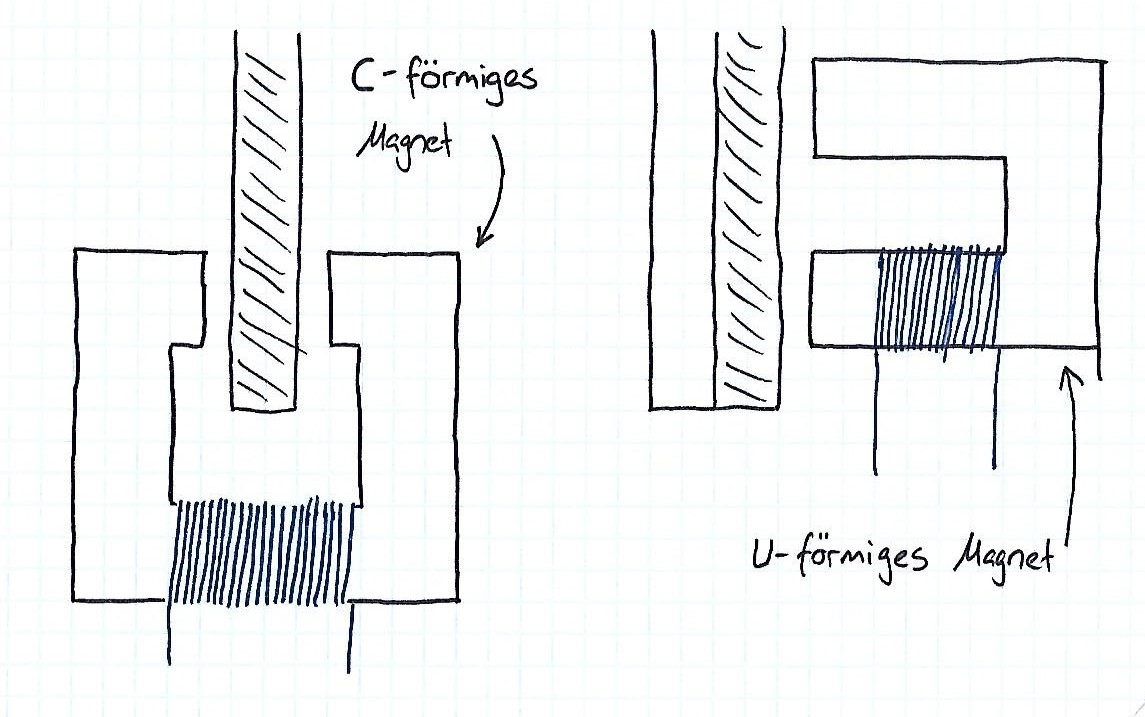
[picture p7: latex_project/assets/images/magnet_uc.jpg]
      
    \end{center}
    \vspace{-3ex}
    \caption{U-förmiges und C-Förmiges Magnet}
    \label{fig:magnet_uc}
  \end{figure}

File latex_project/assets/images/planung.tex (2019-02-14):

\begin{figure}[ht]
    \begin{center}
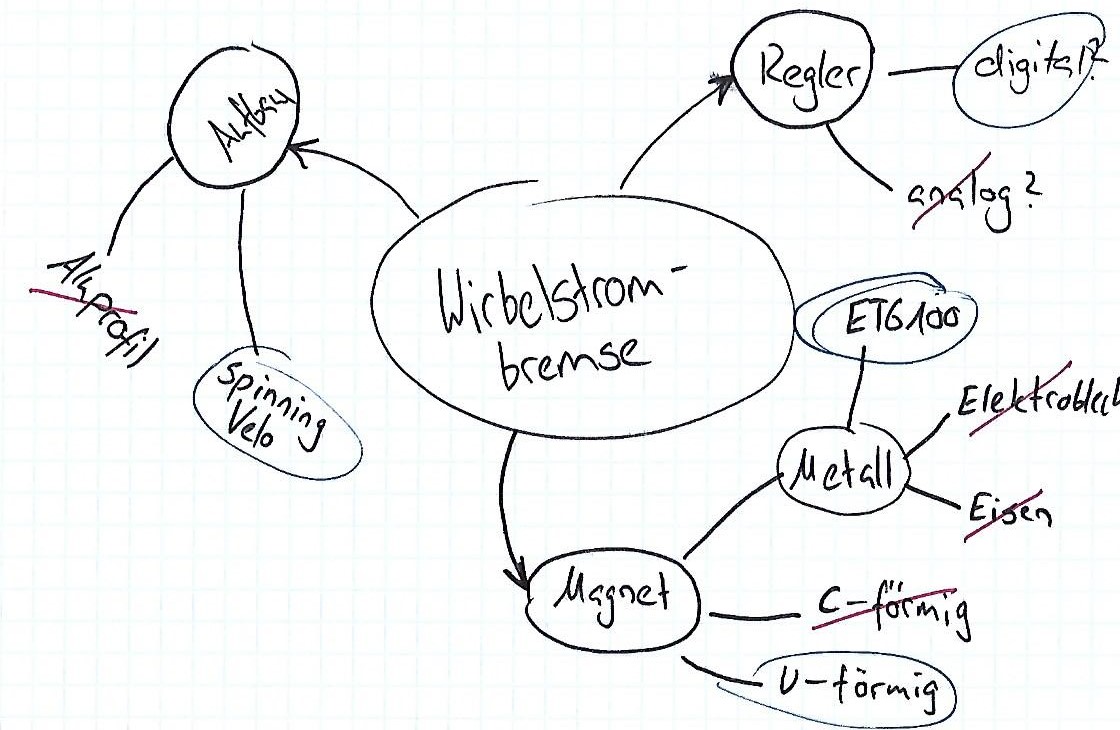
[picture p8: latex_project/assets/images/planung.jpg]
      
    \end{center}
    \vspace{-3ex}
    \caption{Mindmap}
    \label{fig:mindmap}
  \end{figure}

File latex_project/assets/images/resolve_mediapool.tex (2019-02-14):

\begin{figure}[ht]
    \begin{center}
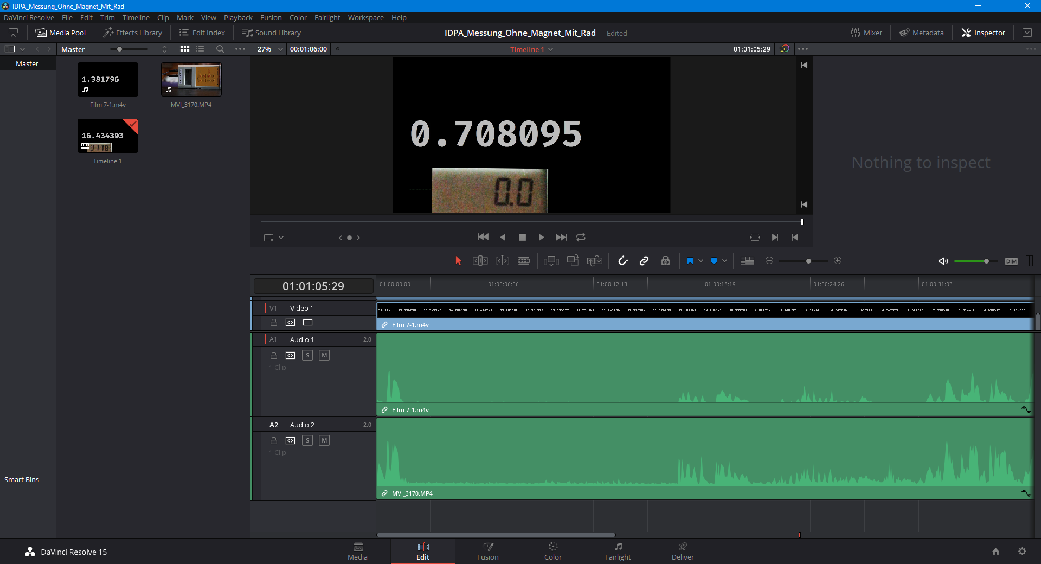
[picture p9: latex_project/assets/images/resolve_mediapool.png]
      
    \end{center}
    \vspace{-3ex}
    \caption{Ausschnitt aus Davinci Resolve}
    \label{fig:resolve_mediapool}
  \end{figure}

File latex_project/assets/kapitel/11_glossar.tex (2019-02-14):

\setglossarystyle{altlisthypergroup}
\printglossary
\glsaddallunused

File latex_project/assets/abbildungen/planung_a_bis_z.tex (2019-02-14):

\begin{figure}[ht]
    \begin{center}
      \begin{tikzpicture}
        \node[emptynode]     (a)                                           {A};
        \node[emptynode]     (z)   [right= 5cm of a]                     {Z};

        \draw [arrow_right] (a) -- (z);

      \end{tikzpicture}
    \end{center}
    \vspace{-3ex}
    \caption{Einfache Vorgehensweise}
    \label{fig:planung_a_bis_z}
  \end{figure}

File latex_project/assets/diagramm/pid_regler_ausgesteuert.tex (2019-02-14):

\begin{figure}[h]
  \begin{center}
    \begin{tikzpicture}
      \begin{axis}[
        axis_regulator_style,
               %title      = P-Regler mit konstanter Abweichung,
               ylabel     = {},
        ylabel near ticks, 
        yticklabel pos        = left,
        minor      grid style = {dashed,gray},
                   xmax       = 110,
                   xlabel     = {t},
                   xticklabels    = {,,},
        legend     style      = {draw=none}
      ]
        \addplot[line_blue] table[x=time,y=pid,col sep=comma,mark=none]{assets/diagramm/pid_regler_ausgesteuert.csv}; 
        \addlegendentry{P + I + D}
      
        \addplot[line_red] table[x=time,y=e,col sep=comma,mark=none]{assets/diagramm/pid_regler_ausgesteuert.csv};        
        \addlegendentry{Abweichung}
        
      \end{axis}
    \end{tikzpicture}
  \end{center}
  \vspace{-3ex}
  
  \caption{PID-Regler mit Schwingungen}
  \label{fig:plot_pid_regulator_out_of_control}
\end{figure}

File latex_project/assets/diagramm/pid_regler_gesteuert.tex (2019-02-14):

\begin{figure}[h]
  \begin{center}
    \begin{tikzpicture}
      \begin{axis}[
        axis_regulator_style,
               %title      = P-Regler mit konstanter Abweichung,
               ylabel     = {},
        ylabel near ticks, 
        yticklabel pos        = left,
        minor      grid style = {dashed,gray},
                   ymax       = 1.5,
                   ymin       = -0.5,
                   xmax       = 110,
                   xlabel     = {t},
                   xticklabels    = {,,},
        legend     style      = {draw=none}
      ]
      
        \addplot[line_red] table[x=time,y=e,col sep=comma,mark=none]{assets/diagramm/pid_regler_gesteuert.csv};    
        \addlegendentry{Abweichung}
        
        \addplot[line_blue] table[x=time,y=pid,col sep=comma,mark=none]{assets/diagramm/pid_regler_gesteuert.csv}; 
        \addlegendentry{P + I + D}
      \end{axis}
    \end{tikzpicture}
  \end{center}
  \vspace{-3ex}
  
  \caption{PID-Regler mit Rückkopplung}
  \label{fig:plot_pid_regulator_controlled}
\end{figure}

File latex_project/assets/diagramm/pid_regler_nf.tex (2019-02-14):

\begin{figure}[h]
  \begin{center}
    \begin{tikzpicture}
      \begin{axis}[
        axis_regulator_style,
               %title         = P-Regler mit konstanter Abweichung,
               ylabel         = {},
        ylabel near ticks, 
        yticklabel pos        = left,
        minor      grid style = {dashed,gray},
                   ymax       = 4,
                   ymin       = -0.5,
                   xmax       = 110,
                   xlabel     = {t},
                   xticklabels    = {,,},
        legend     style      = {draw=none}
      ]
      
        \addplot[line_red] table[x= time,y= e,col sep=comma,mark=none]{assets/diagramm/pi_regler_nf.csv};        
        \addlegendentry{Abweichung}
      
        \addplot[line_blue] table[x= time,y=pid,col sep=comma,mark=none]{assets/diagramm/pid_regler_nf.csv}; 
        \addlegendentry{P + I + D}
      \end{axis}
    \end{tikzpicture}
  \end{center}
  \vspace{-3ex}
  
  \caption{PID-Regler mit konstanter Abweichung}
  \label{fig:plot_pid_regulator_no_feedback}
\end{figure}

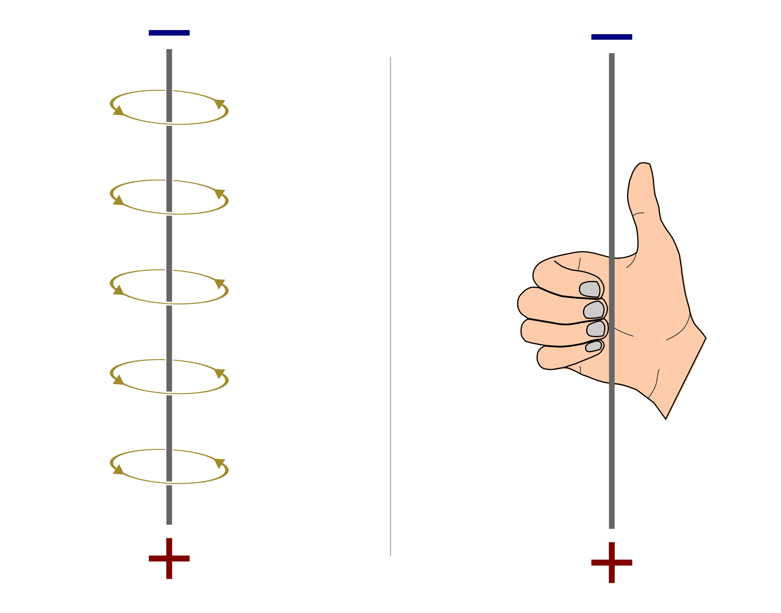
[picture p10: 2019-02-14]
latex_project/assets/images/magnetismus/magnetfeld-leiter-rechte-hand-regel.png

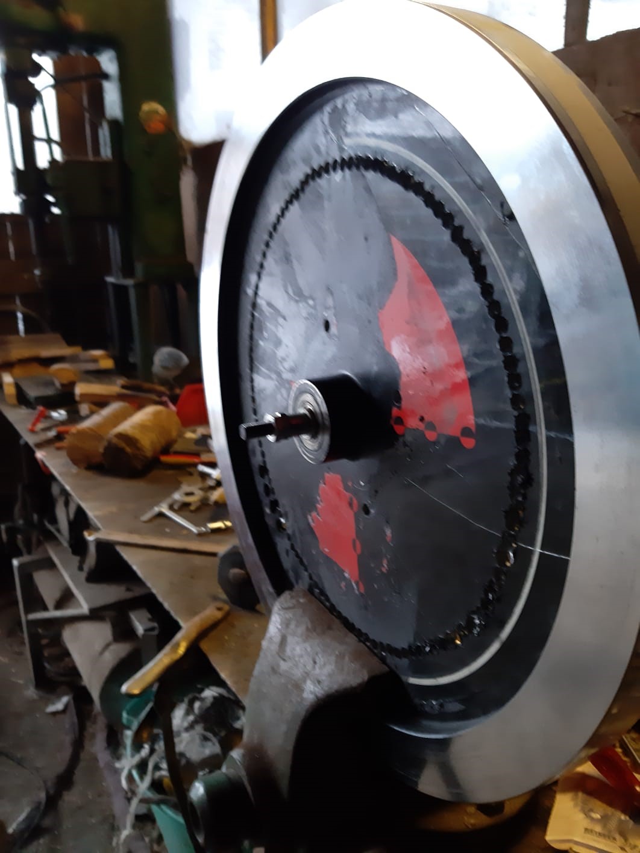
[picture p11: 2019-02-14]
latex_project/assets/images/rad.png

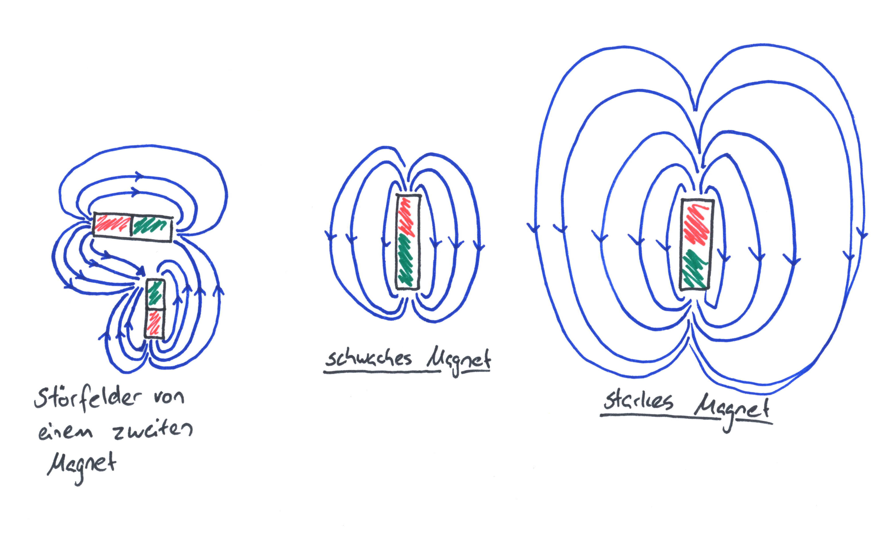
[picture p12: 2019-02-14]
latex_project/assets/images/magnetismus/beeinflussungen_magnet.jpg

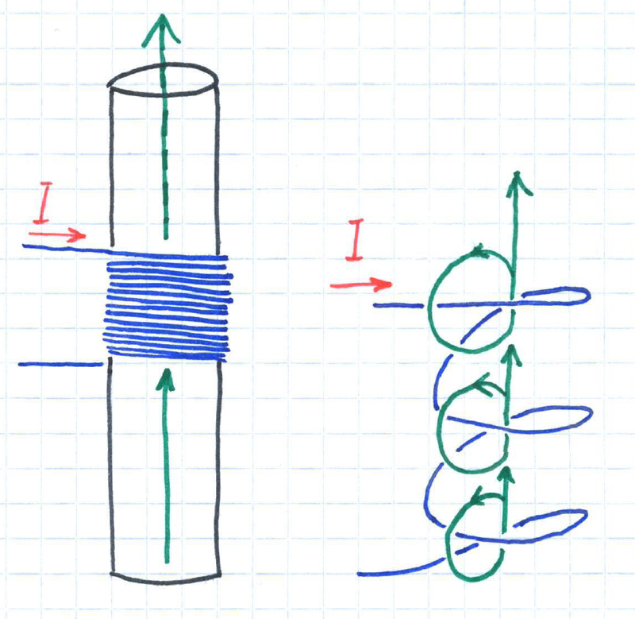
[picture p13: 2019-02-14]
latex_project/assets/images/magnetismus/flussrichtung.PNG

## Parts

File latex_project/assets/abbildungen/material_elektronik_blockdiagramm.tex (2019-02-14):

\begin{figure}[ht]
    \begin{center}
      \begin{tikzpicture}
        \node[labelbox]     (mcu)                                           {MCU};
        \node[labelbox]     (fet)  [right= 2cm of mcu]    {MOSFET};
        \node[labelbox]     (usb)   [above = 2cm of mcu]    {USB};
        \node[emptynode]    (sens)  [left=2cm of mcu]  {Sensor};
  
        \draw [arrow_right] (sens) -- (mcu);
        \draw [arrow_right] (mcu) -- (fet);
        \draw [arrow_right] (mcu) -- (usb);
  
      \end{tikzpicture}
    \end{center}
    \vspace{-3ex}
    \caption{Schaltung Blockdiagramm}
    \label{fig:electronic_block}
  \end{figure}

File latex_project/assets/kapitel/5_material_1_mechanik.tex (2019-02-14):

\subsection{Mechanik}
Die Hauptbedingung an das mechanische Gestell war, dass es ein drehbares Rad aufweisen soll, welches leicht in Bewegung gebracht werden kann. Ausserdem muss sich das Rad auch über eine längere Zeit selbst drehen können. Diese Bedingungen führten dazu, ein Spinning Wheel zu beziehen. Solch ein Spinning Wheel wird als Fitnessgerät verwendet. 
\newpara
Bei der Bremsscheibe wurde eine Aluminium-Scheibe verbaut. Dieses Metall wurde verwendet, da dies einen guten elektrischen Leitwert aufweist und somit auch gute Bremseigenschaften mit sich bringt. Ausserdem besitzt Aluminium als Leichtmetall ein relativ geringes spezifisches Gewicht.
\newpara
Hinter der Aluminium Scheibe befindet sich eine zweite, dickere Scheibe aus Automatenstahl. Hier wurde ETG 100 Automatenstahl verbaut, weil sich dieser leicht magnetisieren lässt und das Magetfeld vergleichsweise gut leiten kann.
\newpara
Als Haltegestell für den Elektromagneten wurden zwei parallel geführte C-Schienen verwendet, damit der Abstand zwischen dem Elektromagneten und der Bremsscheibe variiert werden kann. Ein ausserdem positiver Aspekt der C-Schienen ist, dass diese aus Aluminium bestehen und somit den Elektromagneten, ferromagnetisch von dem Eisengestell trennen. Somit kann eine höhere Wirkungskraft aus dem Magneten erzielt werden. Damit der Elektromagnet an seiner rechten Stelle bleibt, wurde dieser mit Schnellverlegern auf die Schiene geschraubt. Diese Schnellverleger ermöglichen ein rasches bewegen – und fixieren von dem Magnet. 
\newpara
Damit diese zwei C-Schienen sich in einer stabilen und korrekten Lage befinden, wurde ein Gestell gefertigt und die Schienen montiert. Dieses wurde aus dicken Blechplatten konstruiert. Aufgrund einer starken mechanischen Festigkeit wurde jenes Material verbaut. Dieses Eisengestell wurde mit Nieten an das Spinning Wheel gefügt.

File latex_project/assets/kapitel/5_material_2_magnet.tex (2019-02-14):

\subsection{Magnet}
Wichtiger Bestandteil eines Magneten ist das Metall. Das Metall muss ferromagnetisch sein, damit es etwas anziehen kann. Die Magnetisierbarkeit ist abhängig vom Eiseninhalt des Metalls. Je mehr Eisen das Metall hat, desto stärker wird das Magnetfeld bei gleichem Volumen sein (\cite{schulmaterial_magnetismus}). Also war das Ziel der Metall-Wahl, ein Metall herauszusuchen, welches sich für das magnetische Bremsen eignet.
\newpara

\newpara
Für diese Arbeit wurde das Metall \textbf{ETG-100} verwendet. Die Wahl wurde mit Hilfe einer externen Person ausgewählt, weil diese Person sich für das Thema interessierte und bereits selbst Wirbelstrombremsen entworfen hatte.
\newpara
Die Permeabilitätszahl, welche für den Magneten benötigt wird, konnte nur anhand einer Annahme gesetzt werden. Anhand eines Physikbuches wurde der Bereich für ferromagnetische Stoffe 300 bis 10'000 vorgenommen (\cite[S.661]{kuchling2014taschenbuch}). Als Annahme wurde daraus die Permeabilitätszahl 5'000 gesetzt.

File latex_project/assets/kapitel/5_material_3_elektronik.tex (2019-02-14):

\subsection{Elektronik} \label{cap:material_electronics}
Für die richtige Wahl der Komponenten mussten zuerst Voraussetzungen gesetzt werden. Die Voraussetzungen der Elektronik ist das Messen der Geschwindigkeit des Rades, die Regelung der Bremse und eine Möglichkeit die gemessenen Daten auslesen zu können. 

\input{assets/abbildungen/material_elektronik_blockdiagramm.tex}

Der Regler konnte daraus in drei Blöcken aufgeteilt werden: USB, Mikrocontroller und MOSFET. Mit dem USB war das Ziel, Daten auslesen zu können und den Sollwert zu setzen. Der Mikrocontroller würde als Sensor und Gehirn der Elektronik dienen und wäre für das Messen der Geschwindigkeit, die Ansteuerung des Magneten und das Berechnen der Regelung würde der Mikrocontroller zuständig. Der MOSFET dient als Schalter um den Magneten anzusteuern.
\newpara
In den folgenden Unterkapiteln werden die Auswahl und die Begründung der ausgewählten Komponenten aufgeführt.

\subsubsection{Mikrocontroller}
Die wichtigste Komponente ist der Mikrocontroller, welcher einen grossen Anteil an Arbeit übernehmen muss, welche das Messen und das Regeln beinhalten. Zum Messen der Geschwindigkeit und für die Regelung des Magneten werden Timer benötigt. Timer sind in der Elektronik Peripherien, welche mit Events verknüpft werden können. Es ist also möglich einen Event mit einem Timer zu verknüpfen, damit Prozesse, welche einen gleichmässigen Takt benötigen, zuverlässig ausgeführt werden. Der Regler verwendet einen Timer, damit das Integral und das Differenzial mit einer konstanten Abtastrate berechnet werden können. Dies hat den Vorteil, dass die Berechnungen einfacher und genauer berechnet werden können.
\newpara
Ein Interrupt-System dient zur Verknüpfung von Events mit verschiedenen Peripherien. Bei der Bremse wurde ein solches System eingebaut, damit die Geschwindigkeitsmessung genauer berechnet werden kann. Ein Interrupt selbst ist ein Unterbruch im Prozess, welcher von Peripherien ausgelöst werden kann. Bei einem Interrupt wird der aktuelle Prozess gestoppt und ein anderer Prozess wird ausgeführt. Am Ende dieses Prozesses wird wieder mit dem normalen Prozess weitergemacht.
\newpara
Die wichtigsten Kriterien für den Mikrocontroller, aus dem oberen Ausschnitt hergeleitet, sind die Geschwindigkeit des Controllers, Timer Peripherie und ein Interrupt-System. Der Speicherplatz ist ebenfalls wichtig, da das Programm gross werden kann. Zusätzlich hätte ein FPU noch einberechnet werden können, aber dies würde den Controller teurer machen und wird bereits mit der Controllergeschwindigkeit kompensiert. 
\newpara
Aus Familiarität wurde ein Mikrocontroller der Firma Microchip ausgewählt. Neben der Familiarität existiert bereits eine grosse Community, welche Mikrocontroller verwenden und daher auch Dokumentationen von vielen Funktionen existieren. Aus Recherche und eigener Erfahrung konnten zwei Mikrocontroller ausgewählt werden: Atmega328P und Atmega328PB. Beide sind im Aufbau sehr ähnlich, ausser dass der Atmega328PB einige Verbesserungen besitzt.
\newpara
Für das Projekt wurde der \textbf{Atmega328PB} ausgewählt, weil er bessere Timer besitzt, welche länger laufen können, was zu weniger Belastung des Mikrocontrollers führt.
\subsubsection{USB}
Die Aufgabe eines USB-Chips ist es, eine Verbindung zwischen einem Computer und einer Elektronik zu erstellen, damit ein Datenaustausch ausgeführt werden kann. In unserem Fall ist es der Datenaustausch von Geschwindigkeitsmessung.
\newpara
Als USB-Schnittstellen-Chip wurde der \textbf{FT232RL} von FTDI ausgewählt. Dieser wurde ausgewählt, da bereits gute Erfahrungen mit diesem Chip gemacht wurden. Wenn ein anderer Chip ausgewählt würde, müsste man zuerst sich über die elektronischen Verbindungen informieren (wo muss mit was verbunden werden).

\subsubsection{MOSFET}
Ein MOSFET ist ein elektronischer Schalter. Im Vergleich zum normalen mechanischen Schalter, welche von Hand betätigt werden kann, wird der MOSFET via einem elektronischen Signal betätigt.
\newpara
Bei der Auswahl des MOSFETs muss auf die Belastbarkeit und Grösse geachtet werden. Unter Belastbarkeit ist die maximale Zufuhr von elektronischer Energie gemeint. Bei zu grosser Energie kann es sein, dass der MOSFET explodiert und grossen Schaden an der Elektronik anrichtet. Als Grenzwerte wurde die minimale Belastbarkeit für den Magneten auf 2A begrenzt und die Grösse auf Maximum 2 x 2cm begrenzt. Zur Auswahl standen die folgende MOSFETs:
\newpage
\begin{itemize}
    \item CSD18511 von Texas Instruments
    \item Si4436DY von Vishay
    \item CPH6442 von ON-Semiconductor
\end{itemize}

Für das Projekt wurde der \textbf{CPH6442} ausgewählt. Die Begründung ist die Grösse des Bausteins. In einem 2.8mm x 2.9mm Gehäuse kann dieser Chip eine Belastung von maximal 6A aushalten, was genügend für das Magnet ist. Die maximale Spannung beträgt 60V und ist auch für den Magneten geeignet, da der Widerstand der Wicklung klein ist und daher bei 2A eine kleine Spannung erzeugt. Die anderen Bausteine besassen ähnlichen Attributen, scheiterten aber bei der Grösse.

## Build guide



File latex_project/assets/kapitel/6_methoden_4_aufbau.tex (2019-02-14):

\subsection{Aufbau} \label{cap:methoden_aufbau}

Der Aufbau setzt sich aus sich aus folgenden Elementen zusammen: 
\begin{itemize}
\item Elektromagnet		
\item C-Schienen	
\item Aluminumscheibe	
\item ETG-100 Scheibe
\item Gestell für den Elektromagnet
\end{itemize}

Die ETG-100 Scheibe wird als erstes an das Schwungrad montiert. Auf die ETG-100 Platte folgt direkt die Aluminiumscheibe. Diese Armatur wurde starr verschraubt. 
Auf die Stand-Eisenträger des Spinning Wheels wurde das Gestell für den Elektromagneten fixiert. Auf dieses Gestell wurden die zwei C-Schienen angeschgraubt. Auf den C-Schienen wurde der Elektromagnet montiert. Dieser U-förmige Magnet schaut anschliessend mit den Pol-Austritten genau auf die Aluminiumscheibe zu. Die Wicklungen wurden über die Zylinder des Elektromagneten angebracht (Abbildung \ref{fig:gesamtaufbau}).

\begin{figure}[ht]
  \begin{center}
    
  \end{center}
  \vspace{-3ex}
  \caption{Gesamtaufbau}
  \label{fig:gesamtaufbau}
\end{figure}

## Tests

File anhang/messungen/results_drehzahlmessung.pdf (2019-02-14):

index | electronic | mess | mess_converted ratio_el_me | time
1 | 3.987241 | 221.2 | 3.687 | 1.082 | 0.267
2 | 4.093529 | 221.2 | 3.687 | 1.110 | 0.533
3 | 4.228115 | 239.5 | 3.992 | 1.059 | 0.800
4 | 4.374912 | 239.5 | 3.992 | 1.096 | 1.067
5 | 4.477398 | 239.5 | 3.992 | 1.122 | 1.333
6 | 4.524723 | 239.5 | 3.992 | 1.134 | 1.600
7 | 4.638907 | 263.9 | 4.398 | 1.055 | 1.867
8 | 4.771721 | 263.9 | 4.398 | 1.085 | 2.133
9 | 4.901192 | 263.9 | 4.398 | 1.114 | 2.400
10 | 4.968598 | 263.9 | 4.398 | 1.130 | 2.667
11 | 5.20573 | 289.3 | 4.822 | 1.080 | 2.933
12 | 5.257845 | 289.3 | 4.822 | 1.090 | 3.200
13 | 5.377269 | 289.3 | 4.822 | 1.115 | 3.467
14 | 5.531463 | 289.3 | 4.822 | 1.147 | 3.733
15 | 5.660207 | 320.8 | 5.347 | 1.059 | 4.000
16 | 5.775806 | 320.8 | 5.347 | 1.080 | 4.267
17 | 5.909607 | 320.8 | 5.347 | 1.105 | 4.533
18 | 5.998081 | 320.8 | 5.347 | 1.122 | 4.800
19 | 6.12565 | 350.6 | 5.843 | 1.048 | 5.067
20 | 6.216432 | 350.6 | 5.843 | 1.064 | 5.333
21 | 6.349045 | 350.6 | 5.843 | 1.087 | 5.600
22 | 6.533556 | 350.6 | 5.843 | 1.118 | 5.867
23 | 6.693799 | 378.8 | 6.313 | 1.060 | 6.133
24 | 6.903026 | 378.8 | 6.313 | 1.093 | 6.400
25 | 7.00437 | 378.8 | 6.313 | 1.109 | 6.667
26 | 7.181432 | 378.8 | 6.313 | 1.138 | 6.933
27 | 7.363336 | 414.6 | 6.910 | 1.066 | 7.200
28 | 7.551045 | 414.6 | 6.910 | 1.093 | 7.467
29 | 7.707485 | 414.6 | 6.910 | 1.115 | 7.733
30 | 7.959755 | 414.6 | 6.910 | 1.152 | 8.000
31 | 8.113722 | 456.3 | 7.605 | 1.067 | 8.267
32 | 8.280339 | 456.3 | 7.605 | 1.089 | 8.533
33 | 8.435686 | 456.3 | 7.605 | 1.109 | 8.800
34 | 8.583986 | 456.3 | 7.605 | 1.129 | 9.067
35 | 8.832674 | 497.4 | 8.290 | 1.065 | 9.333
36 | 8.963143 | 497.4 | 8.290 | 1.081 | 9.600
37 | 9.199293 | 497.4 | 8.290 | 1.110 | 9.867
38 | 9.296445 | 497.4 | 8.290 | 1.121 | 10.133
39 | 9.540527 | 538.6 | 8.977 | 1.063 | 10.400
40 | 9.612427 | 538.6 | 8.977 | 1.071 | 10.667
41 | 9.78397 | 538.6 | 8.977 | 1.090 | 10.933
42 | 9.847172 | 538.6 | 8.977 | 1.097 | 11.200
43 | 9.928514 | 575.7 | 9.595 | 1.035 | 11.467
44 | 10.024058 | 575.7 | 9.595 | 1.045 | 11.733
45 | 10.092039 | 575.7 | 9.595 | 1.052 | 12.000
46 | 10.199086 | 575.7 | 9.595 | 1.063 | 12.267
47 | 10.229133 | 599.8 | 9.997 | 1.023 | 12.533

48 | 10.200751 | 599.8 | 9.997 | 1.020 | 12.800
49 | 10.18247 | 599.8 | 9.997 | 1.019 | 13.067
50 | 10.155996 | 599.8 | 9.997 | 1.016 | 13.333
51 | 10.131302 | 599.8 | 9.997 | 1.013 | 13.600
52 | 10.1149 | 612.2 | 10.203 | 0.991 | 13.867
53 | 10.08878 | 612.2 | 10.203 | 0.989 | 14.133
54 | 10.06441 | 612.2 | 10.203 | 0.986 | 14.400
55 | 10.0466 | 612.2 | 10.203 | 0.985 | 14.667
56 | 10.0224 | 607.2 | 10.120 | 0.990 | 14.933
57 | 9.9984015 | 607.2 | 10.120 | 0.988 | 15.200
58 | 9.9808375 | 607.2 | 10.120 | 0.986 | 15.467
59 | 9.9569855 | 607.2 | 10.120 | 0.984 | 15.733
60 | 9.9332495 | 601.6 | 10.027 | 0.991 | 16.000
61 | 9.9159135 | 601.6 | 10.027 | 0.989 | 16.267
62 | 9.8923715 | 601.6 | 10.027 | 0.987 | 16.533
63 | 9.8689405 | 601.6 | 10.027 | 0.984 | 16.800
64 | 9.8518295 | 596.5 | 9.942 | 0.991 | 17.067
65 | 9.8285895 | 596.5 | 9.942 | 0.989 | 17.333
66 | 9.8054605 | 596.5 | 9.942 | 0.986 | 17.600
67 | 9.7885675 | 596.5 | 9.942 | 0.985 | 17.867
68 | 9.7640995 | 591.6 | 9.860 | 0.990 | 18.133
69 | 9.7488695 | 591.6 | 9.860 | 0.989 | 18.400
70 | 9.7245995 | 591.6 | 9.860 | 0.986 | 18.667
71 | 9.70045 | 586.8 | 9.780 | 0.992 | 18.933
72 | 9.68242 | 586.8 | 9.780 | 0.990 | 19.200
73 | 9.65549 | 586.8 | 9.780 | 0.987 | 19.467
74 | 9.6391125 | 586.8 | 9.780 | 0.986 | 19.733
75 | 9.61243 | 582 | 9.700 | 0.991 | 20.000
76 | 9.59472 | 582 | 9.700 | 0.989 | 20.267
77 | 9.5697445 | 582 | 9.700 | 0.987 | 20.533
78 | 9.5434425 | 582 | 9.700 | 0.984 | 20.800
79 | 9.5274395 | 576.8 | 9.613 | 0.991 | 21.067
80 | 9.5013685 | 576.8 | 9.613 | 0.988 | 21.333
81 | 9.4855065 | 576.8 | 9.613 | 0.987 | 21.600
82 | 9.4610965 | 576.8 | 9.613 | 0.984 | 21.867
83 | 9.4439405 | 571.6 | 9.527 | 0.991 | 22.133
84 | 9.4254265 | 571.6 | 9.527 | 0.989 | 22.400
85 | 9.4183245 | 571.6 | 9.527 | 0.989 | 22.667
86 | 9.4041535 | 571.6 | 9.527 | 0.987 | 22.933
87 | 9.3970835 | 566.7 | 9.445 | 0.995 | 23.200
88 | 9.3843845 | 566.7 | 9.445 | 0.994 | 23.467
89 | 9.3773445 | 566.7 | 9.445 | 0.993 | 23.733
90 | 9.3646985 | 566.7 | 9.445 | 0.991 | 24.000
91 | 9.3576895 | 563.8 | 9.397 | 0.996 | 24.267
92 | 9.3450965 | 563.8 | 9.397 | 0.995 | 24.533
93 | 9.3381155 | 563.8 | 9.397 | 0.994 | 24.800
94 | 9.3255745 | 563.8 | 9.397 | 0.992 | 25.067
95 | 9.3186235 | 561.4 | 9.357 | 0.996 | 25.333

96 | 9.3047495 | 561.4 | 9.357 | 0.994 | 25.600
97 | 9.2978285 | 561.4 | 9.357 | 0.994 | 25.867
98 | 9.2853965 | 561.4 | 9.357 | 0.992 | 26.133
99 | 9.2785035 | 559 | 9.317 | 0.996 | 26.400
100 | 9.2647505 | 559 | 9.317 | 0.994 | 26.667
101 | 9.2578885 | 559 | 9.317 | 0.994 | 26.933
102 | 9.2496675 | 559 | 9.317 | 0.993 | 27.200
103 | 9.2373645 | 556.6 | 9.277 | 0.996 | 27.467
104 | 9.2291795 | 556.6 | 9.277 | 0.995 | 27.733
105 | 9.2169295 | 556.6 | 9.277 | 0.994 | 28.000
106 | 9.2087815 | 556.6 | 9.277 | 0.993 | 28.267
107 | 9.1979395 | 554.2 | 9.237 | 0.996 | 28.533
108 | 9.1898255 | 554.2 | 9.237 | 0.995 | 28.800
109 | 9.1776805 | 554.2 | 9.237 | 0.994 | 29.067
110 | 9.1696005 | 554.2 | 9.237 | 0.993 | 29.333
111 | 9.1615365 | 551.8 | 9.197 | 0.996 | 29.600
112 | 9.1494665 | 551.8 | 9.197 | 0.995 | 29.867
113 | 9.1414375 | 551.8 | 9.197 | 0.994 | 30.133
114 | 9.1294185 | 551.8 | 9.197 | 0.993 | 30.400
115 | 9.1214255 | 549.4 | 9.157 | 0.996 | 30.667
116 | 9.1094595 | 549.4 | 9.157 | 0.995 | 30.933
117 | 9.1015015 | 549.4 | 9.157 | 0.994 | 31.200
118 | 9.0895865 | 549.4 | 9.157 | 0.993 | 31.467
119 | 9.0816625 | 547 | 9.117 | 0.996 | 31.733
120 | 9.0737512 | 547 | 9.117 | 0.995 | 32.000
121 | 9.0605975 | 547 | 9.117 | 0.994 | 32.267
122 | 9.0527235 | 547 | 9.117 | 0.993 | 32.533
123 | 9.0409375 | 547 | 9.117 | 0.992 | 32.800
124 | 9.0330975 | 544.6 | 9.077 | 0.995 | 33.067
125 | 9.02527 | 544.6 | 9.077 | 0.994 | 33.333
126 | 9.0122575 | 544.6 | 9.077 | 0.993 | 33.600
127 | 9.0031695 | 542.2 | 9.037 | 0.996 | 33.867
128 | 8.9928055 | 542.2 | 9.037 | 0.995 | 34.133
129 | 8.9850495 | 542.2 | 9.037 | 0.994 | 34.400
130 | 8.9760165 | 542.2 | 9.037 | 0.993 | 34.667
131 | 8.9644295 | 539.9 | 8.998 | 0.996 | 34.933
132 | 8.9554385 | 539.9 | 8.998 | 0.995 | 35.200
133 | 8.9439045 | 539.9 | 8.998 | 0.994 | 35.467
134 | 8.9362315 | 539.9 | 8.998 | 0.993 | 35.733
135 | 8.9285715 | 537.7 | 8.962 | 0.996 | 36.000
136 | 8.9158345 | 537.7 | 8.962 | 0.995 | 36.267
137 | 8.9082105 | 537.7 | 8.962 | 0.994 | 36.533
138 | 8.8955315 | 537.7 | 8.962 | 0.993 | 36.800
139 | 8.8879405 | 535.5 | 8.925 | 0.996 | 37.067
140 | 8.8791025 | 535.5 | 8.925 | 0.995 | 37.333
141 | 8.8677645 | 535.5 | 8.925 | 0.994 | 37.600
142 | 8.8589655 | 535.5 | 8.925 | 0.993 | 37.867
143 | 8.8514385 | 533.4 | 8.890 | 0.996 | 38.133

144 | 8.8401695 | 533.4 | 8.890 | 0.994 | 38.400
145 | 8.8314265 | 533.4 | 8.890 | 0.993 | 38.667
146 | 8.8227005 | 533.4 | 8.890 | 0.992 | 38.933
147 | 8.8102625 | 531.2 | 8.853 | 0.995 | 39.200
148 | 8.8028165 | 531.2 | 8.853 | 0.994 | 39.467
149 | 8.7941475 | 531.2 | 8.853 | 0.993 | 39.733
150 | 8.7817905 | 529 | 8.817 | 0.996 | 40.000
151 | 8.7743935 | 529 | 8.817 | 0.995 | 40.267
152 | 8.7657785 | 529 | 8.817 | 0.994 | 40.533
153 | 8.7510505 | 529 | 8.817 | 0.993 | 40.800
154 | 8.7437055 | 526.7 | 8.778 | 0.996 | 41.067
155 | 8.7302695 | 526.7 | 8.778 | 0.995 | 41.333
156 | 8.7168765 | 526.7 | 8.778 | 0.993 | 41.600
157 | 8.7059485 | 526.7 | 8.778 | 0.992 | 41.867
158 | 8.6962585 | 524.6 | 8.743 | 0.995 | 42.133
159 | 8.6841745 | 524.6 | 8.743 | 0.993 | 42.400
160 | 8.6745315 | 524.6 | 8.743 | 0.992 | 42.667
161 | 8.6649105 | 524.6 | 8.743 | 0.991 | 42.933
162 | 8.6541135 | 521.3 | 8.688 | 0.996 | 43.200
163 | 8.6445375 | 521.3 | 8.688 | 0.995 | 43.467
164 | 8.6373685 | 521.3 | 8.688 | 0.994 | 43.733
165 | 8.6290215 | 521.3 | 8.688 | 0.993 | 44.000
166 | 8.6171245 | 519.4 | 8.657 | 0.995 | 44.267
167 | 8.6076305 | 519.4 | 8.657 | 0.994 | 44.533
168 | 8.6005235 | 519.4 | 8.657 | 0.994 | 44.800
169 | 8.5875245 | 519.4 | 8.657 | 0.992 | 45.067
170 | 8.5792725 | 517 | 8.617 | 0.996 | 45.333
171 | 8.5710365 | 517 | 8.617 | 0.995 | 45.600
172 | 8.5569545 | 517 | 8.617 | 0.993 | 45.867
173 | 8.5487625 | 517 | 8.617 | 0.992 | 46.133
174 | 8.5394185 | 514.8 | 8.580 | 0.995 | 46.400
175 | 8.5324235 | 514.8 | 8.580 | 0.994 | 46.667
176 | 8.5184685 | 514.8 | 8.580 | 0.993 | 46.933
177 | 8.5115085 | 514.8 | 8.580 | 0.992 | 47.200
178 | 8.5034015 | 512.6 | 8.543 | 0.995 | 47.467
179 | 8.4953115 | 512.6 | 8.543 | 0.994 | 47.733
180 | 8.4826275 | 512.6 | 8.543 | 0.993 | 48.000
181 | 8.4711305 | 512.6 | 8.543 | 0.992 | 48.267
182 | 8.4619555 | 510.3 | 8.505 | 0.995 | 48.533
183 | 8.4482295 | 510.3 | 8.505 | 0.993 | 48.800
184 | 8.4402445 | 510.3 | 8.505 | 0.992 | 49.067
185 | 8.4322725 | 510.3 | 8.505 | 0.991 | 49.333
186 | 8.4243165 | 507.9 | 8.465 | 0.995 | 49.600
187 | 8.4118435 | 507.9 | 8.465 | 0.994 | 49.867
188 | 8.4039265 | 507.9 | 8.465 | 0.993 | 50.133
189 | 8.3948965 | 505.5 | 8.425 | 0.996 | 50.400
190 | 8.3881365 | 505.5 | 8.425 | 0.996 | 50.667
191 | 8.3780165 | 505.5 | 8.425 | 0.994 | 50.933

192 | 8.3656815 | 505.5 | 8.425 | 0.993 | 51.200
193 | 8.3578495 | 503.3 | 8.388 | 0.996 | 51.467
194 | 8.3500345 | 503.3 | 8.388 | 0.995 | 51.733
195 | 8.3422325 | 503.3 | 8.388 | 0.995 | 52.000
196 | 8.3288915 | 503.3 | 8.388 | 0.993 | 52.267
197 | 8.3211295 | 503.3 | 8.388 | 0.992 | 52.533
198 | 8.3122755 | 501.1 | 8.352 | 0.995 | 52.800
199 | 8.3034415 | 501.1 | 8.352 | 0.994 | 53.067
200 | 8.2902245 | 501.1 | 8.352 | 0.993 | 53.333
201 | 8.2836315 | 501.1 | 8.352 | 0.992 | 53.600
202 | 8.2748585 | 498.8 | 8.313 | 0.995 | 53.867
203 | 8.2661025 | 498.8 | 8.313 | 0.994 | 54.133
204 | 8.2584575 | 498.8 | 8.313 | 0.993 | 54.400
205 | 8.2497365 | 498.8 | 8.313 | 0.992 | 54.667
206 | 8.2377765 | 496.5 | 8.275 | 0.996 | 54.933
207 | 8.2290985 | 496.5 | 8.275 | 0.994 | 55.200
208 | 8.2193585 | 496.5 | 8.275 | 0.993 | 55.467
209 | 8.2128775 | 496.5 | 8.275 | 0.992 | 55.733
210 | 8.2031765 | 494.4 | 8.240 | 0.996 | 56.000
211 | 8.1913505 | 494.4 | 8.240 | 0.994 | 56.267
212 | 8.1816995 | 494.4 | 8.240 | 0.993 | 56.533
213 | 8.1731405 | 494.4 | 8.240 | 0.992 | 56.800
214 | 8.1645985 | 492 | 8.200 | 0.996 | 57.067
215 | 8.1560755 | 492 | 8.200 | 0.995 | 57.333
216 | 8.1433235 | 492 | 8.200 | 0.993 | 57.600
217 | 8.1337845 | 492 | 8.200 | 0.992 | 57.867
218 | 8.1253255 | 489.7 | 8.162 | 0.996 | 58.133
219 | 8.1179375 | 489.7 | 8.162 | 0.995 | 58.400
220 | 8.1084595 | 489.7 | 8.162 | 0.993 | 58.667
221 | 8.1000525 | 489.7 | 8.162 | 0.992 | 58.933
222 | 8.0916625 | 487.4 | 8.123 | 0.996 | 59.200
223 | 8.0791105 | 487.4 | 8.123 | 0.995 | 59.467
224 | 8.0697225 | 487.4 | 8.123 | 0.993 | 59.733
225 | 8.0592964 | 487.4 | 8.123 | 0.992 | 60.000

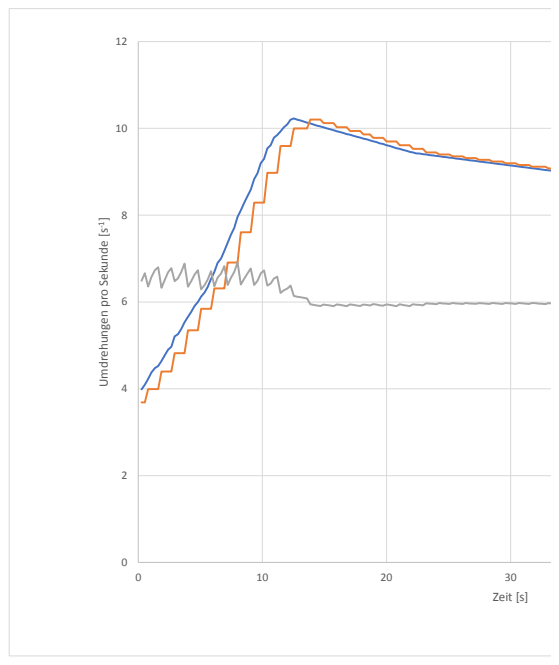
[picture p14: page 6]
Zeit [s]

Umdrehungen pro Sekunde [s-1]

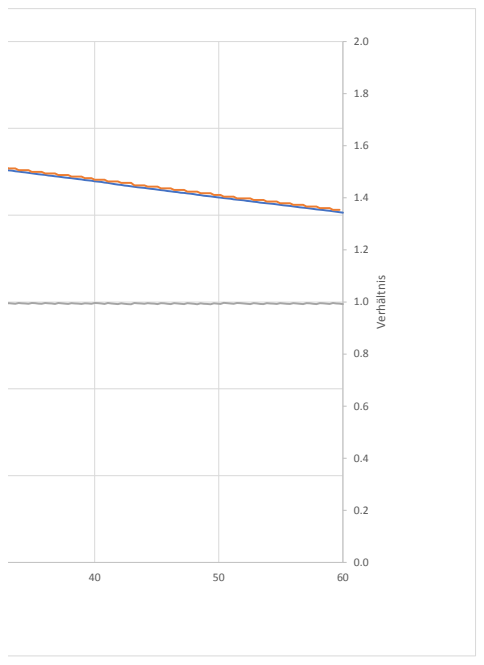
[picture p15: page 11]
Verhältnis

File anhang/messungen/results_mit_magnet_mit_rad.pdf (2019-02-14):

index | electronic | mess | mess_convertedratio_el_me | time
1 | 15.184645 | 936.7 15.61166667 | 0.972647272 | 0.133
2 | 15.147842 | 936.7 15.61166667 | 0.970289869 | 0.267
3 | 15.107566 | 919.5 | 15.325 | 0.985811811 | 0.400
4 | 15.071136 | 919.5 | 15.325 | 0.983434649 | 0.533
5 | 15.027652 | 919.5 | 15.325 | 0.980597194 | 0.667
6 | 14.991604 | 919.5 | 15.325 | 0.978244959 | 0.800
7 | 14.952152 | 919.5 | 15.325 | 0.975670604 | 0.933
8 | 14.916469 | 919.5 | 15.325 | 0.973342186 | 1.067
9 | 14.880951 | 919.5 | 15.325 | 0.971024535 | 1.200
10 | 14.84208 | 919.5 | 15.325 | 0.968488091 | 1.333
11 | 14.796401 | 901.5 | 15.025 | 0.984785424 | 1.467
12 | 14.754485 | 901.5 | 15.025 | 0.981995674 | 1.600
13 | 14.719735 | 901.5 | 15.025 | 0.979682862 | 1.733
14 | 14.685151 | 901.5 | 15.025 | 0.977381098 | 1.867
15 | 14.647293 | 901.5 | 15.025 | 0.974861431 | 2.000
16 | 14.606217 | 901.5 | 15.025 | 0.972127587 | 2.133
17 | 14.572161 | 901.5 | 15.025 | 0.969860965 | 2.267
18 | 14.531505 | 901.5 | 15.025 | 0.967155075 | 2.400
19 | 14.494433 | 883.5 | 14.725 | 0.9843418 | 2.533
20 | 14.474295 | 883.5 | 14.725 | 0.982974194 | 2.667
21 | 14.43418 | 883.5 | 14.725 | 0.980249915 | 2.800
22 | 14.387661 | 883.5 | 14.725 | 0.97709073 | 2.933
23 | 14.348025 | 883.5 | 14.725 | 0.974398981 | 3.067
24 | 14.308607 | 883.5 | 14.725 | 0.971722037 | 3.200
25 | 14.26615 | 883.5 | 14.725 | 0.96883871 | 3.333
26 | 14.22718 | 883.5 | 14.725 | 0.96619219 | 3.467
27 | 14.188421 | 866.2 14.43666667 | 0.982804502 | 3.600
28 | 14.149876 | 866.2 14.43666667 | 0.980134565 | 3.733
29 | 14.108352 | 866.2 14.43666667 | 0.977258278 | 3.867
30 | 14.092446 | 866.2 14.43666667 | 0.9761565 | 4.000
31 | 14.054419 | 866.2 14.43666667 | 0.973522443 | 4.133
32 | 14.01974 | 866.2 14.43666667 | 0.971120296 | 4.267
33 | 13.982102 | 866.2 14.43666667 | 0.968513184 | 4.400
34 | 13.944667 | 866.2 14.43666667 | 0.965920134 | 4.533
35 | 13.907432 | 848.1 | 14.135 | 0.983900389 | 4.667
36 | 13.864242 | 848.1 | 14.135 | 0.980844853 | 4.800
37 | 13.842746 | 848.1 | 14.135 | 0.979324089 | 4.933
38 | 13.806053 | 848.1 | 14.135 | 0.976728192 | 5.067
39 | 13.76652 | 848.1 | 14.135 | 0.973931376 | 5.200
40 | 13.65225 | 848.1 | 14.135 | 0.965847188 | 5.333
41 | 13.516437 | 848.1 | 14.135 | 0.956238911 | 5.467
42 | 13.368984 | 831.3 | 13.855 | 0.964921256 | 5.600
43 | 13.300703 | 831.3 | 13.855 | 0.959992999 | 5.733
44 | 13.155127 | 831.3 | 13.855 | 0.94948589 | 5.867
45 | 13.009993 | 831.3 | 13.855 | 0.939010682 | 6.000
46 | 12.937281 | 831.3 | 13.855 | 0.933762613 | 6.133
47 | 12.783801 | 831.3 | 13.855 | 0.922685023 | 6.267
48 | 12.631367 | 831.3 | 13.855 | 0.91168293 | 6.400
49 | 12.480032 | 831.3 | 13.855 | 0.900760159 | 6.533

50 | 12.400794 | 787.6 13.12666667 | 0.944702438 | 6.667
51 | 12.242899 | 787.6 13.12666667 | 0.93267387 | 6.800
52 | 12.1619 | 787.6 13.12666667 | 0.926503301 | 6.933
53 | 12.000769 | 787.6 13.12666667 | 0.914228212 | 7.067
54 | 11.837122 | 787.6 13.12666667 | 0.901761453 | 7.200
55 | 11.754749 | 787.6 13.12666667 | 0.895486211 | 7.333
56 | 11.586949 | 787.6 13.12666667 | 0.882703073 | 7.467
57 | 11.49954 | 787.6 13.12666667 | 0.876044185 | 7.600
58 | 11.326569 | 725.4 | 12.09 | 0.936854342 | 7.733
59 | 11.238986 | 725.4 | 12.09 | 0.929610091 | 7.867
60 | 11.063905 | 725.4 | 12.09 | 0.915128619 | 8.000
61 | 10.97454 | 725.4 | 12.09 | 0.907736973 | 8.133
62 | 10.790746 | 725.4 | 12.09 | 0.892534822 | 8.267
63 | 10.698391 | 725.4 | 12.09 | 0.884895864 | 8.400
64 | 10.511268 | 725.4 | 12.09 | 0.869418362 | 8.533
65 | 10.416667 | 725.4 | 12.09 | 0.861593631 | 8.667
66 | 10.31864 | 661.8 | 11.03 | 0.9355068 | 8.800
67 | 10.124737 | 661.8 | 11.03 | 0.917927199 | 8.933
68 | 10.024058 | 661.8 | 11.03 | 0.908799456 | 9.067
69 | 9.926938 | 661.8 | 11.03 | 0.899994379 | 9.200
70 | 9.822411 | 661.8 | 11.03 | 0.89051777 | 9.333
71 | 9.616864 | 661.8 | 11.03 | 0.871882502 | 9.467
72 | 9.510042 | 661.8 | 11.03 | 0.862197824 | 9.600
73 | 9.404153 | 661.8 | 11.03 | 0.852597733 | 9.733
74 | 9.184423 | 599.5 9.991666667 | 0.919208307 | 9.867
75 | 9.073751 | 599.5 9.991666667 | 0.908131877 | 10.000
76 | 8.960573 | 599.5 9.991666667 | 0.896804637 | 10.133
77 | 8.843923 | 599.5 9.991666667 | 0.885129908 | 10.267
78 | 8.730269 | 599.5 9.991666667 | 0.873755029 | 10.400
79 | 8.613561 | 599.5 9.991666667 | 0.862074495 | 10.533
80 | 8.378016 | 599.5 9.991666667 | 0.83850035 | 10.667
81 | 8.258457 | 538.8 | 8.98 | 0.91965 | 10.800
82 | 8.131668 | 538.8 | 8.98 | 0.905530958 | 10.933
83 | 8.008714 | 538.8 | 8.98 | 0.891838976 | 11.067
84 | 7.878482 | 538.8 | 8.98 | 0.877336526 | 11.200
85 | 7.748574 | 538.8 | 8.98 | 0.862870156 | 11.333
86 | 7.617306 | 538.8 | 8.98 | 0.848252339 | 11.467
87 | 7.481445 | 538.8 | 8.98 | 0.833123051 | 11.600
88 | 7.345163 | 538.8 | 8.98 | 0.817946882 | 11.733
89 | 7.205441 | 477.8 7.963333333 | 0.90482725 | 11.867
90 | 7.059753 | 477.8 7.963333333 | 0.886532398 | 12.000
91 | 6.913717 | 477.8 7.963333333 | 0.868193847 | 12.133
92 | 6.766265 | 477.8 7.963333333 | 0.84967748 | 12.267
93 | 6.766265 | 477.8 7.963333333 | 0.84967748 | 12.400
94 | 6.613757 | 477.8 7.963333333 | 0.830526203 | 12.533
95 | 6.460616 | 477.8 7.963333333 | 0.811295437 | 12.667
96 | 6.301674 | 477.8 7.963333333 | 0.791336208 | 12.800
97 | 6.138283 | 416.4 | 6.94 | 0.884478818 | 12.933
98 | 5.978002 | 416.4 | 6.94 | 0.861383573 | 13.067
99 | 5.978002 | 416.4 | 6.94 | 0.861383573 | 13.200

100 | 5.811251 | 416.4 | 6.94 | 0.837356052 | 13.333
101 | 5.63825 | 416.4 | 6.94 | 0.812427954 | 13.467
102 | 5.468067 | 416.4 | 6.94 | 0.787905908 | 13.600
103 | 5.468067 | 416.4 | 6.94 | 0.787905908 | 13.733
104 | 5.285412 | 355.5 | 5.925 | 0.892052658 | 13.867
105 | 5.101624 | 355.5 | 5.925 | 0.861033586 | 14.000
106 | 5.101624 | 355.5 | 5.925 | 0.861033586 | 14.133
107 | 4.91971 | 355.5 | 5.925 | 0.830330802 | 14.267
108 | 4.724469 | 355.5 | 5.925 | 0.797378734 | 14.400
109 | 4.724469 | 355.5 | 5.925 | 0.797378734 | 14.533
110 | 4.527673 | 355.5 | 5.925 | 0.764164219 | 14.667
111 | 4.527673 | 297.2 4.953333333 | 0.914065882 | 14.800
112 | 4.326158 | 297.2 4.953333333 | 0.873383176 | 14.933
113 | 4.326158 | 297.2 4.953333333 | 0.873383176 | 15.067
114 | 4.106709 | 297.2 4.953333333 | 0.829079879 | 15.200
115 | 4.106709 | 297.2 4.953333333 | 0.829079879 | 15.333
116 | 3.884883 | 297.2 4.953333333 | 0.784296703 | 15.467
117 | 3.884883 | 297.2 4.953333333 | 0.784296703 | 15.600
118 | 3.653048 | 297.2 4.953333333 | 0.737492867 | 15.733
119 | 3.653048 | 297.2 4.953333333 | 0.737492867 | 15.867
120 | 3.406923 | 297.2 4.953333333 | 0.687804105 | 16.000
121 | 3.406923 | 235 3.916666667 | 0.869852681 | 16.133
122 | 3.154017 | 235 3.916666667 | 0.805280936 | 16.267
123 | 3.154017 | 235 3.916666667 | 0.805280936 | 16.400
124 | 3.154017 | 235 3.916666667 | 0.805280936 | 16.533
125 | 2.890307 | 235 3.916666667 | 0.737950723 | 16.667
126 | 2.890307 | 235 3.916666667 | 0.737950723 | 16.800
127 | 2.890307 | 235 3.916666667 | 0.737950723 | 16.933
128 | 2.618898 | 235 3.916666667 | 0.668654809 | 17.067
129 | 2.618898 | 177 | 2.95 | 0.887762034 | 17.200
130 | 2.618898 | 177 | 2.95 | 0.887762034 | 17.333
131 | 2.351304 | 177 | 2.95 | 0.797052203 | 17.467
132 | 2.351304 | 177 | 2.95 | 0.797052203 | 17.600
133 | 2.351304 | 177 | 2.95 | 0.797052203 | 17.733
134 | 2.058562 | 177 | 2.95 | 0.697817627 | 17.867
135 | 2.058562 | 177 | 2.95 | 0.697817627 | 18.000
136 | 2.058562 | 177 | 2.95 | 0.697817627 | 18.133
137 | 2.058562 | 177 | 2.95 | 0.697817627 | 18.267
138 | 2.058562 | 177 | 2.95 | 0.697817627 | 18.400
139 | 1.735388 | 177 | 2.95 | 0.588267119 | 18.533
140 | 1.735388 | 126.5 2.108333333 | 0.823108933 | 18.667
141 | 1.735388 | 126.5 2.108333333 | 0.823108933 | 18.800
142 | 1.735388 | 126.5 2.108333333 | 0.823108933 | 18.933
143 | 1.735388 | 126.5 2.108333333 | 0.823108933 | 19.067
144 | 1.407182 | 126.5 2.108333333 | 0.667438103 | 19.200
145 | 1.407182 | 126.5 2.108333333 | 0.667438103 | 19.333
146 | 1.407182 | 126.5 2.108333333 | 0.667438103 | 19.467
147 | 1.407182 | 126.5 2.108333333 | 0.667438103 | 19.600
148 | 1.407182 | 126.5 2.108333333 | 0.667438103 | 19.733
149 | 1.407182 | 126.5 2.108333333 | 0.667438103 | 19.867

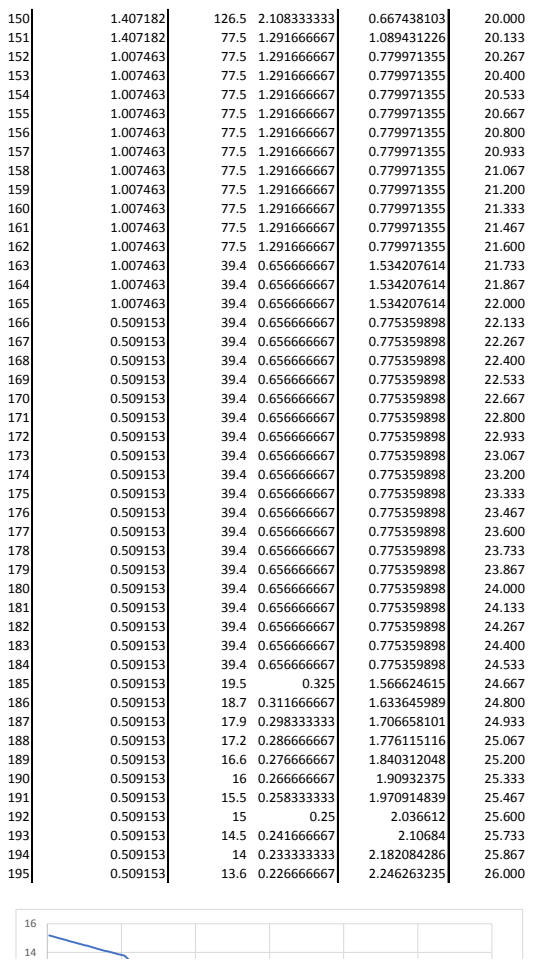
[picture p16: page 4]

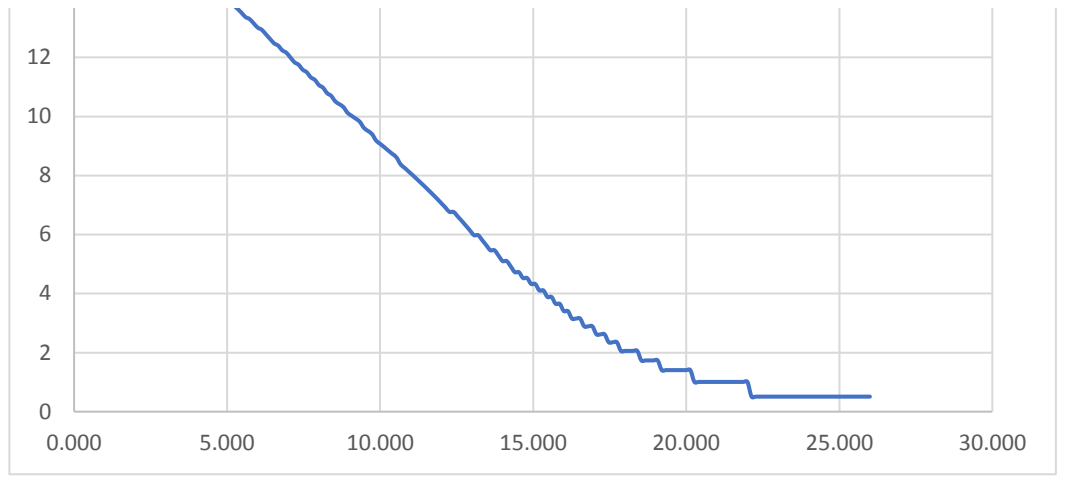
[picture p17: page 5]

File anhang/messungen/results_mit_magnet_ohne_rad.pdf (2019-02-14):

index | electronic | mess | mess_converted ratio_el_me | time
1 | 11.24303 | 682.8 | 11.380 | 0.9880 | 0.533
2 | 11.172686 | 682.8 | 11.380 | 0.9818 | 1.067
3 | 11.103216 | 674.5 | 11.242 | 0.9877 | 1.600
4 | 11.032658 | 674.5 | 11.242 | 0.9814 | 2.133
5 | 10.961066 | 666.2 | 11.103 | 0.9872 | 2.667
6 | 10.8904 | 662.3 | 11.038 | 0.9866 | 3.200
7 | 10.83189 | 658.1 | 10.968 | 0.9876 | 3.733
8 | 10.759168 | 650.3 | 10.838 | 0.9927 | 4.267
9 | 10.687415 | 650.3 | 10.838 | 0.9861 | 4.800
10 | 10.613008 | 642.4 | 10.707 | 0.9913 | 5.333
11 | 10.552086 | 642.4 | 10.707 | 0.9856 | 5.867
12 | 10.479545 | 634.3 | 10.572 | 0.9913 | 6.400
13 | 10.416667 | 634.3 | 10.572 | 0.9853 | 6.933
14 | 10.342546 | 626.2 | 10.437 | 0.9910 | 7.467
15 | 10.281297 | 626.2 | 10.437 | 0.9851 | 8.000
16 | 10.204082 | 618 | 10.300 | 0.9907 | 8.533
17 | 10.142811 | 618 | 10.300 | 0.9847 | 9.067
18 | 10.066033 | 609.7 | 10.162 | 0.9906 | 9.600
19 | 10.0016 | 609.7 | 10.162 | 0.9842 | 10.133
20 | 9.936407 | 601.3 | 10.022 | 0.9915 | 10.667
21 | 9.858045 | 601.3 | 10.022 | 0.9837 | 11.200
22 | 9.794703 | 593.2 | 9.887 | 0.9907 | 11.733
23 | 9.72914 | 593.2 | 9.887 | 0.9841 | 12.267
24 | 9.662956 | 585.4 | 9.757 | 0.9904 | 12.800
25 | 9.596192 | 585.4 | 9.757 | 0.9836 | 13.333
26 | 9.528892 | 577.4 | 9.623 | 0.9902 | 13.867
27 | 9.462528 | 577.4 | 9.623 | 0.9833 | 14.400
28 | 9.394258 | 569.4 | 9.490 | 0.9899 | 14.933
29 | 9.325574 | 569.4 | 9.490 | 0.9827 | 15.467
30 | 9.257888 | 561.3 | 9.355 | 0.9896 | 16.000
31 | 9.188474 | 561.3 | 9.355 | 0.9822 | 16.533
32 | 9.118763 | 553 | 9.217 | 0.9894 | 17.067
33 | 9.048791 | 553 | 9.217 | 0.9818 | 17.600
34 | 8.978595 | 544.7 | 9.078 | 0.9890 | 18.133
35 | 8.90821 | 544.7 | 9.078 | 0.9813 | 18.667
36 | 8.851438 | 536.7 | 8.945 | 0.9895 | 19.200
37 | 8.779323 | 536.7 | 8.945 | 0.9815 | 19.733
38 | 8.707161 | 529 | 8.817 | 0.9876 | 20.267
39 | 8.648126 | 529 | 8.817 | 0.9809 | 20.800
40 | 8.574565 | 521.1 | 8.685 | 0.9873 | 21.333
41 | 8.514986 | 521.1 | 8.685 | 0.9804 | 21.867
42 | 8.441383 | 513.2 | 8.553 | 0.9869 | 22.400
43 | 8.381387 | 513.2 | 8.553 | 0.9799 | 22.933
44 | 8.306751 | 505.2 | 8.420 | 0.9866 | 23.467
45 | 8.245382 | 505.2 | 8.420 | 0.9793 | 24.000
46 | 8.183842 | 497.1 | 8.285 | 0.9878 | 24.533
47 | 8.107407 | 497.1 | 8.285 | 0.9786 | 25.067
48 | 8.044794 | 488.9 | 8.148 | 0.9873 | 25.600
49 | 7.984159 | 488.9 | 8.148 | 0.9799 | 26.133

50 | 7.904388 | 480.5 | 8.008 | 0.9870 | 26.667
51 | 7.841907 | 480.5 | 8.008 | 0.9792 | 27.200
52 | 7.777501 | 472.5 | 7.875 | 0.9876 | 27.733
53 | 7.713192 | 472.5 | 7.875 | 0.9795 | 28.267
54 | 7.648066 | 464.8 | 7.747 | 0.9873 | 28.800
55 | 7.584031 | 464.8 | 7.747 | 0.9790 | 29.333
56 | 7.518344 | 457.1 | 7.618 | 0.9869 | 29.867
57 | 7.452009 | 457.1 | 7.618 | 0.9782 | 30.400
58 | 7.385088 | 449.2 | 7.487 | 0.9864 | 30.933
59 | 7.318501 | 449.2 | 7.487 | 0.9775 | 31.467
60 | 7.251421 | 441.3 | 7.355 | 0.9859 | 32.000
61 | 7.183908 | 441.3 | 7.355 | 0.9767 | 32.533
62 | 7.115209 | 433.2 | 7.220 | 0.9855 | 33.067
63 | 7.062944 | 433.2 | 7.220 | 0.9782 | 33.600
64 | 6.994181 | 425 | 7.083 | 0.9874 | 34.133
65 | 6.923673 | 425 | 7.083 | 0.9775 | 34.667
66 | 6.853821 | 417.1 | 6.952 | 0.9859 | 35.200
67 | 6.80087 | 417.1 | 6.952 | 0.9783 | 35.733
68 | 6.729113 | 409.8 | 6.830 | 0.9852 | 36.267
69 | 6.675211 | 409.8 | 6.830 | 0.9773 | 36.800
70 | 6.603275 | 402.3 | 6.705 | 0.9848 | 37.333
71 | 6.548617 | 402.3 | 6.705 | 0.9767 | 37.867
72 | 6.474672 | 394.7 | 6.578 | 0.9842 | 38.400
73 | 6.419474 | 394.7 | 6.578 | 0.9759 | 38.933
74 | 6.344534 | 387 | 6.450 | 0.9836 | 39.467
75 | 6.288992 | 387 | 6.450 | 0.9750 | 40.000
76 | 6.231928 | 379.1 | 6.318 | 0.9863 | 40.533
77 | 6.15521 | 379.1 | 6.318 | 0.9742 | 41.067
78 | 6.098156 | 371.2 | 6.187 | 0.9857 | 41.600
79 | 6.039231 | 371.2 | 6.187 | 0.9762 | 42.133
80 | 5.982007 | 363.1 | 6.052 | 0.9885 | 42.667
81 | 5.923048 | 363.1 | 6.052 | 0.9787 | 43.200
82 | 5.843853 | 355.5 | 5.925 | 0.9863 | 43.733
83 | 5.748359 | 355.5 | 5.925 | 0.9702 | 44.267
84 | 5.723968 | 348.4 | 5.807 | 0.9858 | 44.800
85 | 5.663284 | 348.4 | 5.807 | 0.9753 | 45.333
86 | 5.601864 | 341.2 | 5.687 | 0.9851 | 45.867
87 | 5.54078 | 341.2 | 5.687 | 0.9743 | 46.400
88 | 5.478611 | 333.9 | 5.565 | 0.9845 | 46.933
89 | 5.417353 | 333.9 | 5.565 | 0.9735 | 47.467
90 | 5.374957 | 326.4 | 5.440 | 0.9880 | 48.000
91 | 5.312367 | 326.4 | 5.440 | 0.9765 | 48.533
92 | 5.248132 | 318.9 | 5.315 | 0.9874 | 49.067
93 | 5.184141 | 318.9 | 5.315 | 0.9754 | 49.600
94 | 5.119174 | 318.9 | 5.315 | 0.9632 | 50.133
95 | 5.076348 | 311.2 | 5.187 | 0.9787 | 50.667
96 | 5.010823 | 311.2 | 5.187 | 0.9661 | 51.200
97 | 4.945403 | 303.5 | 5.058 | 0.9777 | 51.733
98 | 4.900807 | 303.5 | 5.058 | 0.9689 | 52.267
99 | 4.834842 | 296.2 | 4.937 | 0.9794 | 52.800

100 | 4.789639 | 296.2 | 4.937 | 0.9702 | 53.333
101 | 4.722327 | 289.6 | 4.827 | 0.9784 | 53.867
102 | 4.676394 | 289.6 | 4.827 | 0.9689 | 54.400
103 | 4.607785 | 282.8 | 4.713 | 0.9776 | 54.933
104 | 4.561045 | 282.8 | 4.713 | 0.9677 | 55.467
105 | 4.491879 | 276 | 4.600 | 0.9765 | 56.000
106 | 4.445235 | 276 | 4.600 | 0.9664 | 56.533
107 | 4.398001 | 269 | 4.483 | 0.9810 | 57.067
108 | 4.327355 | 269 | 4.483 | 0.9652 | 57.600
109 | 4.279356 | 261.9 | 4.365 | 0.9804 | 58.133
110 | 4.230978 | 261.9 | 4.365 | 0.9693 | 58.667
111 | 4.18284 | 254.8 | 4.247 | 0.9850 | 59.200
112 | 4.109409 | 254.8 | 4.247 | 0.9677 | 59.733
113 | 4.061343 | 247.5 | 4.125 | 0.9846 | 60.267
114 | 4.010266 | 247.5 | 4.125 | 0.9722 | 60.800
115 | 3.96071 | 247.5 | 4.125 | 0.9602 | 61.333
116 | 3.911383 | 240.1 | 4.002 | 0.9774 | 61.867
117 | 3.860646 | 240.1 | 4.002 | 0.9648 | 62.400
118 | 3.809814 | 233.4 | 3.890 | 0.9794 | 62.933
119 | 3.758268 | 233.4 | 3.890 | 0.9661 | 63.467
120 | 3.707438 | 227.3 | 3.788 | 0.9786 | 64.000
121 | 3.656039 | 227.3 | 3.788 | 0.9651 | 64.533
122 | 3.603136 | 221.1 | 3.685 | 0.9778 | 65.067
123 | 3.550935 | 221.1 | 3.685 | 0.9636 | 65.600
124 | 3.498265 | 214.9 | 3.582 | 0.9767 | 66.133
125 | 3.443906 | 214.9 | 3.582 | 0.9615 | 66.667
126 | 3.39121 | 208.5 | 3.475 | 0.9759 | 67.200
127 | 3.363832 | 208.5 | 3.475 | 0.9680 | 67.733
128 | 3.308454 | 202.1 | 3.368 | 0.9822 | 68.267
129 | 3.254869 | 202.1 | 3.368 | 0.9663 | 68.800
130 | 3.226973 | 195.5 | 3.258 | 0.9904 | 69.333
131 | 3.171945 | 195.5 | 3.258 | 0.9735 | 69.867
132 | 3.115187 | 195.5 | 3.258 | 0.9561 | 70.400
133 | 3.08764 | 188.9 | 3.148 | 0.9807 | 70.933
134 | 3.030744 | 188.9 | 3.148 | 0.9627 | 71.467
135 | 2.972651 | 182.1 | 3.035 | 0.9795 | 72.000
136 | 2.945334 | 182.1 | 3.035 | 0.9705 | 72.533
137 | 2.886569 | 176.1 | 2.935 | 0.9835 | 73.067
138 | 2.857796 | 176.1 | 2.935 | 0.9737 | 73.600
139 | 2.798424 | 170.8 | 2.847 | 0.9831 | 74.133
140 | 2.769776 | 170.8 | 2.847 | 0.9730 | 74.667
141 | 2.709733 | 165.6 | 2.760 | 0.9818 | 75.200
142 | 2.679643 | 165.6 | 2.760 | 0.9709 | 75.733
143 | 2.619008 | 160.1 | 2.668 | 0.9815 | 76.267
144 | 2.588527 | 160.1 | 2.668 | 0.9701 | 76.800
145 | 2.557178 | 160.1 | 2.668 | 0.9583 | 77.333
146 | 2.49491 | 154.7 | 2.578 | 0.9676 | 77.867
147 | 2.464025 | 154.7 | 2.578 | 0.9557 | 78.400
148 | 2.434274 | 149.1 | 2.485 | 0.9796 | 78.933
149 | 2.401814 | 149.1 | 2.485 | 0.9665 | 79.467

150 | 2.338022 | 143.5 | 2.392 | 0.9776 | 80.000
151 | 2.304487 | 143.5 | 2.392 | 0.9635 | 80.533
152 | 2.27372 | 143.5 | 2.392 | 0.9507 | 81.067
153 | 2.241831 | 137.6 | 2.293 | 0.9775 | 81.600
154 | 2.2077 | 137.6 | 2.293 | 0.9627 | 82.133
155 | 2.141951 | 131.8 | 2.197 | 0.9751 | 82.667
156 | 2.108423 | 131.8 | 2.197 | 0.9598 | 83.200
157 | 2.07586 | 131.8 | 2.197 | 0.9450 | 83.733
158 | 2.041216 | 125.8 | 2.097 | 0.9736 | 84.267
159 | 2.006421 | 125.8 | 2.097 | 0.9570 | 84.800
160 | 1.972355 | 125.8 | 2.097 | 0.9407 | 85.333
161 | 1.937083 | 119.7 | 1.995 | 0.9710 | 85.867
162 | 1.902877 | 119.7 | 1.995 | 0.9538 | 86.400
163 | 1.869243 | 114.5 | 1.908 | 0.9795 | 86.933
164 | 1.831931 | 114.5 | 1.908 | 0.9600 | 87.467
165 | 1.794997 | 110.3 | 1.838 | 0.9764 | 88.000
166 | 1.75982 | 110.3 | 1.838 | 0.9573 | 88.533
167 | 1.721953 | 105.8 | 1.763 | 0.9765 | 89.067
168 | 1.686955 | 105.8 | 1.763 | 0.9567 | 89.600
169 | 1.650078 | 101.6 | 1.693 | 0.9745 | 90.133
170 | 1.650078 | 101.6 | 1.693 | 0.9745 | 90.667
171 | 1.61534 | 97 | 1.617 | 0.9992 | 91.200
172 | 1.57399 | 97 | 1.617 | 0.9736 | 91.733
173 | 1.535664 | 97 | 1.617 | 0.9499 | 92.267
174 | 1.496791 | 92.5 | 1.542 | 0.9709 | 92.800
175 | 1.496791 | 92.5 | 1.542 | 0.9709 | 93.333
176 | 1.459155 | 87.9 | 1.465 | 0.9960 | 93.867
177 | 1.417266 | 87.9 | 1.465 | 0.9674 | 94.400
178 | 1.376834 | 87.9 | 1.465 | 0.9398 | 94.933
179 | 1.376834 | 83 | 1.383 | 0.9953 | 95.467
180 | 1.337099 | 83 | 1.383 | 0.9666 | 96.000
181 | 1.295203 | 83 | 1.383 | 0.9363 | 96.533
182 | 1.295203 | 78.1 | 1.302 | 0.9950 | 97.067
183 | 1.254642 | 78.1 | 1.302 | 0.9639 | 97.600
184 | 1.21331 | 78.1 | 1.302 | 0.9321 | 98.133
185 | 1.21331 | 73.2 | 1.220 | 0.9945 | 98.667
186 | 1.166807 | 73.2 | 1.220 | 0.9564 | 99.200
187 | 1.12166 | 73.2 | 1.220 | 0.9194 | 99.733
188 | 1.12166 | 67.8 | 1.130 | 0.9926 | 100.267
189 | 1.078349 | 67.8 | 1.130 | 0.9543 | 100.800
190 | 1.078349 | 67.8 | 1.130 | 0.9543 | 101.333
191 | 1.030639 | 67.8 | 1.130 | 0.9121 | 101.867
192 | 1.030639 | 62.3 | 1.038 | 0.9926 | 102.400
193 | 0.985898 | 62.3 | 1.038 | 0.9495 | 102.933
194 | 0.985898 | 58.3 | 0.972 | 1.0146 | 103.467
195 | 0.93706 | 58.3 | 0.972 | 0.9644 | 104.000
196 | 0.93706 | 55.2 | 0.920 | 1.0185 | 104.533
197 | 0.884367 | 55.2 | 0.920 | 0.9613 | 105.067
198 | 0.884367 | 52.1 | 0.868 | 1.0185 | 105.600
199 | 0.837173 | 52.1 | 0.868 | 0.9641 | 106.133

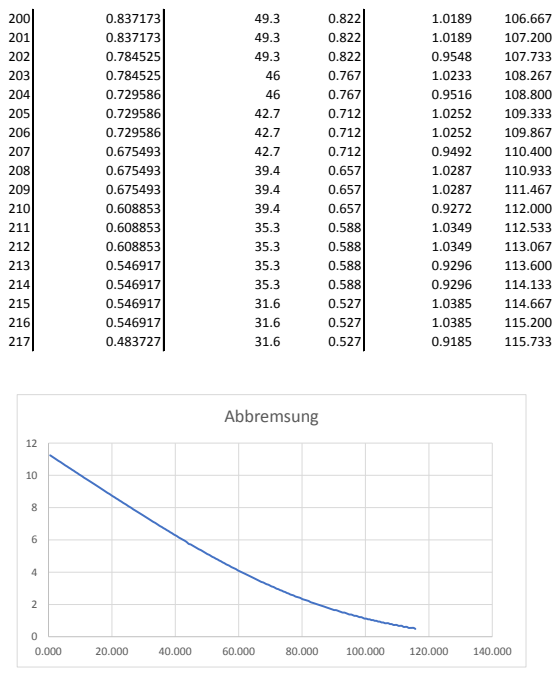
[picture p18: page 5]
Abbremsung

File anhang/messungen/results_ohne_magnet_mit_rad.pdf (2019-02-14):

index | electronic | mess | mess_convertedratio_el_metime
1 | 16.434393 | 977.8 | 16.297 | 1.008 | 0.267 | 0
2 | 16.284523 | 977.8 | 16.297 | 0.999 | 0.533 | 8
3 | 16.133196 | 977.8 | 16.297 | 0.990 | 0.800 | 16
4 | 15.996928 | 983 | 16.383 | 0.976 | 1.067 | 24
5 | 15.862944 | 983 | 16.383 | 0.968 | 1.333 | 32
6 | 15.711412 | 983 | 16.383 | 0.959 | 1.600 | 40
7 | 15.609389 | 983 | 16.383 | 0.953 | 1.867 | 48
8 | 15.524094 | 951.7 | 15.862 | 0.979 | 2.133 | 56
9 | 15.424481 | 951.7 | 15.862 | 0.972 | 2.400 | 64
10 | 15.344954 | 951.7 | 15.862 | 0.967 | 2.667 | 72
11 | 15.269973 | 951.7 | 15.862 | 0.963 | 2.933 | 80
12 | 15.195722 | 926.9 | 15.448 | 0.984 | 3.200 | 88
13 | 15.114873 | 926.9 | 15.448 | 0.978 | 3.467 | 96
14 | 15.027652 | 926.9 | 15.448 | 0.973 | 3.733 | 104
15 | 14.948577 | 926.9 | 15.448 | 0.968 | 4.000 | 112
16 | 14.87387 | 907.6 | 15.127 | 0.983 | 4.267 | 120
17 | 14.789399 | 907.6 | 15.127 | 0.978 | 4.533 | 128
18 | 14.709343 | 907.6 | 15.127 | 0.972 | 4.800 | 136
19 | 14.63015 | 907.6 | 15.127 | 0.967 | 5.067 | 144
20 | 14.548417 | 888.8 | 14.813 | 0.982 | 5.333 | 152
21 | 14.470942 | 888.8 | 14.813 | 0.977 | 5.600 | 160
22 | 14.397605 | 888.8 | 14.813 | 0.972 | 5.867 | 168
23 | 14.318442 | 888.8 | 14.813 | 0.967 | 6.133 | 176
24 | 14.259639 | 870.9 | 14.515 | 0.982 | 6.400 | 184
25 | 14.178765 | 870.9 | 14.515 | 0.977 | 6.667 | 192
26 | 14.086094 | 870.9 | 14.515 | 0.970 | 6.933 | 200
27 | 14.000896 | 870.9 | 14.515 | 0.965 | 7.200 | 208
28 | 13.941557 | 853.3 | 14.222 | 0.980 | 7.467 | 216
29 | 13.858093 | 853.3 | 14.222 | 0.974 | 7.733 | 224
30 | 13.775621 | 853.3 | 14.222 | 0.969 | 8.000 | 232
31 | 13.712155 | 834.9 | 13.915 | 0.985 | 8.267 | 240
32 | 13.631408 | 834.9 | 13.915 | 0.980 | 8.533 | 248
33 | 13.54573 | 834.9 | 13.915 | 0.973 | 8.800 | 256
34 | 13.48145 | 834.9 | 13.915 | 0.969 | 9.067 | 264
35 | 13.394771 | 817.4 | 13.623 | 0.983 | 9.333 | 272
36 | 13.331912 | 817.4 | 13.623 | 0.979 | 9.600 | 280
37 | 13.244332 | 817.4 | 13.623 | 0.972 | 9.867 | 288
38 | 13.177314 | 817.4 | 13.623 | 0.967 | 10.133 | 296
39 | 13.091747 | 799.4 | 13.323 | 0.983 | 10.400 | 304
40 | 13.026261 | 799.4 | 13.323 | 0.978 | 10.667 | 312
41 | 12.937281 | 799.4 | 13.323 | 0.971 | 10.933 | 320
42 | 12.870676 | 799.4 | 13.323 | 0.966 | 11.200 | 328
43 | 12.781186 | 781.1 | 13.018 | 0.982 | 11.467 | 336
44 | 12.716175 | 781.1 | 13.018 | 0.977 | 11.733 | 344
45 | 12.649262 | 781.1 | 13.018 | 0.972 | 12.000 | 352
46 | 12.562815 | 781.1 | 13.018 | 0.965 | 12.267 | 360
47 | 12.495002 | 763.2 | 12.720 | 0.982 | 12.533 | 368
48 | 12.422977 | 763.2 | 12.720 | 0.977 | 12.800 | 376
49 | 12.334716 | 763.2 | 12.720 | 0.970 | 13.067 | 384

50 | 12.266929 | 763.2 | 12.720 | 0.964 | 13.333 | 392
51 | 12.197502 | 745.8 | 12.430 | 0.981 | 13.600 | 400
52 | 12.131212 | 745.8 | 12.430 | 0.976 | 13.867 | 408
53 | 12.035433 | 745.8 | 12.430 | 0.968 | 14.133 | 416
54 | 11.966303 | 745.8 | 12.430 | 0.963 | 14.400 | 424
55 | 11.895699 | 728 | 12.133 | 0.980 | 14.667 | 432
56 | 11.825923 | 728 | 12.133 | 0.975 | 14.933 | 440
57 | 11.754749 | 728 | 12.133 | 0.969 | 15.200 | 448
58 | 11.662624 | 728 | 12.133 | 0.961 | 15.467 | 456
59 | 11.593397 | 710.6 | 11.843 | 0.979 | 15.733 | 464
60 | 11.520738 | 710.6 | 11.843 | 0.973 | 16.000 | 472
61 | 11.446887 | 710.6 | 11.843 | 0.967 | 16.267 | 480
62 | 11.378119 | 710.6 | 11.843 | 0.961 | 16.533 | 488
63 | 11.30199 | 693.6 | 11.560 | 0.978 | 16.800 | 496
64 | 11.228889 | 693.6 | 11.560 | 0.971 | 17.067 | 504
65 | 11.15673 | 693.6 | 11.560 | 0.965 | 17.333 | 512
66 | 11.081561 | 676.3 | 11.272 | 0.983 | 17.600 | 520
67 | 11.007397 | 676.3 | 11.272 | 0.977 | 17.867 | 528
68 | 10.941877 | 676.3 | 11.272 | 0.971 | 18.133 | 536
69 | 10.884709 | 676.3 | 11.272 | 0.966 | 18.400 | 544
70 | 10.809409 | 659.4 | 10.990 | 0.984 | 18.667 | 552
71 | 10.733299 | 659.4 | 10.990 | 0.977 | 18.933 | 560
72 | 10.658254 | 659.4 | 10.990 | 0.970 | 19.200 | 568
73 | 10.580667 | 659.4 | 10.990 | 0.963 | 19.467 | 576
74 | 10.507734 | 642.9 | 10.715 | 0.981 | 19.733 | 584
75 | 10.458501 | 642.9 | 10.715 | 0.976 | 20.000 | 592
76 | 10.383784 | 642.9 | 10.715 | 0.969 | 20.267 | 600
77 | 10.305029 | 642.9 | 10.715 | 0.962 | 20.533 | 608
78 | 10.227459 | 626.3 | 10.438 | 0.980 | 20.800 | 616
79 | 10.177496 | 626.3 | 10.438 | 0.975 | 21.067 | 624
80 | 10.101827 | 626.3 | 10.438 | 0.968 | 21.333 | 632
81 | 10.020844 | 626.3 | 10.438 | 0.960 | 21.600 | 640
82 | 9.94273 | 609.4 | 10.157 | 0.979 | 21.867 | 648
83 | 9.890805 | 609.4 | 10.157 | 0.974 | 22.133 | 656
84 | 9.811617 | 609.4 | 10.157 | 0.966 | 22.400 | 664
85 | 9.754955 | 609.4 | 10.157 | 0.960 | 22.667 | 672
86 | 9.674922 | 592.9 | 9.882 | 0.979 | 22.933 | 680
87 | 9.593246 | 592.9 | 9.882 | 0.971 | 23.200 | 688
88 | 9.537617 | 592.9 | 9.882 | 0.965 | 23.467 | 696
89 | 9.45394 | 592.9 | 9.882 | 0.957 | 23.733 | 704
90 | 9.398497 | 576.7 | 9.612 | 0.978 | 24.000 | 712
91 | 9.314456 | 576.7 | 9.612 | 0.969 | 24.267 | 720
92 | 9.260632 | 576.7 | 9.612 | 0.963 | 24.533 | 728
93 | 9.207425 | 576.7 | 9.612 | 0.958 | 24.800 | 736
94 | 9.121425 | 560.2 | 9.337 | 0.977 | 25.067 | 744
95 | 9.061911 | 560.2 | 9.337 | 0.971 | 25.333 | 752
96 | 8.977305 | 560.2 | 9.337 | 0.962 | 25.600 | 760
97 | 8.920924 | 560.2 | 9.337 | 0.955 | 25.867 | 768
98 | 8.863991 | 543.4 | 9.057 | 0.979 | 26.133 | 776
99 | 8.774393 | 543.4 | 9.057 | 0.969 | 26.400 | 784

100 | 8.716876 | 543.4 | 9.057 | 0.962 | 26.667 | 792
101 | 8.654113 | 543.4 | 9.057 | 0.956 | 26.933 | 800
102 | 8.56399 | 526.9 | 8.782 | 0.975 | 27.200 | 808
103 | 8.504558 | 526.9 | 8.782 | 0.968 | 27.467 | 816
104 | 8.445946 | 526.9 | 8.782 | 0.962 | 27.733 | 824
105 | 8.353381 | 526.9 | 8.782 | 0.951 | 28.000 | 832
106 | 8.291324 | 510.7 | 8.512 | 0.974 | 28.267 | 840
107 | 8.230182 | 510.7 | 8.512 | 0.967 | 28.533 | 848
108 | 8.169934 | 510.7 | 8.512 | 0.960 | 28.800 | 856
109 | 8.107407 | 510.7 | 8.512 | 0.953 | 29.067 | 864
110 | 8.042723 | 494.3 | 8.238 | 0.976 | 29.333 | 872
111 | 7.979063 | 494.3 | 8.238 | 0.969 | 29.600 | 880
112 | 7.88544 | 494.3 | 8.238 | 0.957 | 29.867 | 888
113 | 7.82032 | 494.3 | 8.238 | 0.949 | 30.133 | 896
114 | 7.755304 | 478.3 | 7.972 | 0.973 | 30.400 | 904
115 | 7.690414 | 478.3 | 7.972 | 0.965 | 30.667 | 912
116 | 7.627532 | 478.3 | 7.972 | 0.957 | 30.933 | 920
117 | 7.563838 | 478.3 | 7.972 | 0.949 | 31.200 | 928
118 | 7.494904 | 462.9 | 7.715 | 0.971 | 31.467 | 936
119 | 7.428979 | 462.9 | 7.715 | 0.963 | 31.733 | 944
120 | 7.36594 | 462.9 | 7.715 | 0.955 | 32.000 | 952
121 | 7.296287 | 447.3 | 7.455 | 0.979 | 32.267 | 960
122 | 7.227104 | 447.3 | 7.455 | 0.969 | 32.533 | 968
123 | 7.160861 | 447.3 | 7.455 | 0.961 | 32.800 | 976
124 | 7.124131 | 447.3 | 7.455 | 0.956 | 33.067 | 984
125 | 7.056565 | 447.3 | 7.455 | 0.947 | 33.333 | 992
126 | 6.989487 | 431.1 | 7.185 | 0.973 | 33.600 | 1000
127 | 6.915246 | 431.1 | 7.185 | 0.962 | 33.867 | 1008
128 | 6.846313 | 431.1 | 7.185 | 0.953 | 34.133 | 1016
129 | 6.778006 | 415.5 | 6.925 | 0.979 | 34.400 | 1024
130 | 6.703851 | 415.5 | 6.925 | 0.968 | 34.667 | 1032
131 | 6.668801 | 415.5 | 6.925 | 0.963 | 34.933 | 1040
132 | 6.59561 | 415.5 | 6.925 | 0.952 | 35.200 | 1048
133 | 6.518565 | 400.6 | 6.677 | 0.976 | 35.467 | 1056
134 | 6.448618 | 400.6 | 6.677 | 0.966 | 35.733 | 1064
135 | 6.409599 | 400.6 | 6.677 | 0.960 | 36.000 | 1072
136 | 6.33553 | 400.6 | 6.677 | 0.949 | 36.267 | 1080
137 | 6.260016 | 400.6 | 6.677 | 0.938 | 36.533 | 1088
138 | 6.221382 | 385.1 | 6.418 | 0.969 | 36.800 | 1096
139 | 6.146735 | 385.1 | 6.418 | 0.958 | 37.067 | 1104
140 | 6.104112 | 385.1 | 6.418 | 0.951 | 37.333 | 1112
141 | 6.027582 | 385.1 | 6.418 | 0.939 | 37.600 | 1120
142 | 5.947849 | 369.2 | 6.153 | 0.967 | 37.867 | 1128
143 | 5.907372 | 369.2 | 6.153 | 0.960 | 38.133 | 1136
144 | 5.828593 | 369.2 | 6.153 | 0.947 | 38.400 | 1144
145 | 5.788645 | 369.2 | 6.153 | 0.941 | 38.667 | 1152
146 | 5.70672 | 353.8 | 5.897 | 0.968 | 38.933 | 1160
147 | 5.661745 | 353.8 | 5.897 | 0.960 | 39.200 | 1168
148 | 5.580855 | 353.8 | 5.897 | 0.946 | 39.467 | 1176
149 | 5.536363 | 353.8 | 5.897 | 0.939 | 39.733 | 1184

150 | 5.4528 | 339.2 | 5.653 | 0.965 | 40.000 | 1192
151 | 5.404705 | 339.2 | 5.653 | 0.956 | 40.267 | 1200
152 | 5.320055 | 339.2 | 5.653 | 0.941 | 40.533 | 1208
153 | 5.273817 | 339.2 | 5.653 | 0.933 | 40.800 | 1216
154 | 5.230563 | 323.7 | 5.395 | 0.970 | 41.067 | 1224
155 | 5.137268 | 323.7 | 5.395 | 0.952 | 41.333 | 1232
156 | 5.097879 | 323.7 | 5.395 | 0.945 | 41.600 | 1240
157 | 5.05247 | 323.7 | 5.395 | 0.937 | 41.867 | 1248
158 | 4.959924 | 307.7 | 5.128 | 0.967 | 42.133 | 1256
159 | 4.907735 | 307.7 | 5.128 | 0.957 | 42.400 | 1264
160 | 4.861165 | 307.7 | 5.128 | 0.948 | 42.667 | 1272
161 | 4.768081 | 307.7 | 5.128 | 0.930 | 42.933 | 1280
162 | 4.720901 | 292.5 | 4.875 | 0.968 | 43.200 | 1288
163 | 4.672897 | 292.5 | 4.875 | 0.959 | 43.467 | 1296
164 | 4.619023 | 292.5 | 4.875 | 0.947 | 43.733 | 1304
165 | 4.522758 | 292.5 | 4.875 | 0.928 | 44.000 | 1312
166 | 4.468435 | 278.1 | 4.635 | 0.964 | 44.267 | 1320
167 | 4.418835 | 278.1 | 4.635 | 0.953 | 44.533 | 1328
168 | 4.36483 | 278.1 | 4.635 | 0.942 | 44.800 | 1336
169 | 4.312427 | 278.1 | 4.635 | 0.930 | 45.067 | 1344
170 | 4.266212 | 262.7 | 4.378 | 0.974 | 45.333 | 1352
171 | 4.212158 | 262.7 | 4.378 | 0.962 | 45.600 | 1360
172 | 4.104012 | 262.7 | 4.378 | 0.937 | 45.867 | 1368
173 | 4.045831 | 262.7 | 4.378 | 0.924 | 46.133 | 1376
174 | 3.991825 | 262.7 | 4.378 | 0.912 | 46.400 | 1384
175 | 3.940234 | 246.9 | 4.115 | 0.958 | 46.667 | 1392
176 | 3.878374 | 246.9 | 4.115 | 0.942 | 46.933 | 1400
177 | 3.822162 | 246.9 | 4.115 | 0.929 | 47.200 | 1408
178 | 3.764607 | 246.9 | 4.115 | 0.915 | 47.467 | 1416
179 | 3.702168 | 232 | 3.867 | 0.957 | 47.733 | 1424
180 | 3.650275 | 232 | 3.867 | 0.944 | 48.000 | 1432
181 | 3.586183 | 232 | 3.867 | 0.927 | 48.267 | 1440
182 | 3.520928 | 232 | 3.867 | 0.911 | 48.533 | 1448
183 | 3.462412 | 217.9 | 3.632 | 0.953 | 48.800 | 1456
184 | 3.462412 | 217.9 | 3.632 | 0.953 | 49.067 | 1464
185 | 3.397478 | 217.9 | 3.632 | 0.936 | 49.333 | 1472
186 | 3.334045 | 217.9 | 3.632 | 0.918 | 49.600 | 1480
187 | 3.275167 | 203.1 | 3.385 | 0.968 | 49.867 | 1488
188 | 3.205292 | 203.1 | 3.385 | 0.947 | 50.133 | 1496
189 | 3.133618 | 203.1 | 3.385 | 0.926 | 50.400 | 1504
190 | 3.068991 | 203.1 | 3.385 | 0.907 | 50.667 | 1512
191 | 3.068991 | 203.1 | 3.385 | 0.907 | 50.933 | 1520
192 | 2.99559 | 187.1 | 3.118 | 0.961 | 51.200 | 1528
193 | 2.925893 | 187.1 | 3.118 | 0.938 | 51.467 | 1536
194 | 2.854663 | 187.1 | 3.118 | 0.915 | 51.733 | 1544
195 | 2.854663 | 187.1 | 3.118 | 0.915 | 52.000 | 1552
196 | 2.771127 | 172.3 | 2.872 | 0.965 | 52.267 | 1560
197 | 2.698618 | 172.3 | 2.872 | 0.940 | 52.533 | 1568
198 | 2.622964 | 172.3 | 2.872 | 0.913 | 52.800 | 1576
199 | 2.622964 | 172.3 | 2.872 | 0.913 | 53.067 | 1584
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

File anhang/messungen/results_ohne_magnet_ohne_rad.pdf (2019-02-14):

index | electronic | mess | mess_converted ratio_el_me | time
1 | 6.092212 | 352.3 5.87166667 | 1.037560942 | 1.067 | 0
2 | 6.003843 | 363.7 6.06166667 | 0.990460764 | 2.133 | 32
3 | 5.9682973 | 361.4 6.02333333 | 0.990862861 | 3.200 | 64
4 | 5.9371143 | 358.4 5.97333333 | 0.993936546 | 4.267 | 96
5 | 5.8995663 | 356.4 | 5.94 | 0.99319298 | 5.333 | 128
6 | 5.8668923 | 354.5 5.90833333 | 0.992986003 | 6.400 | 160
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

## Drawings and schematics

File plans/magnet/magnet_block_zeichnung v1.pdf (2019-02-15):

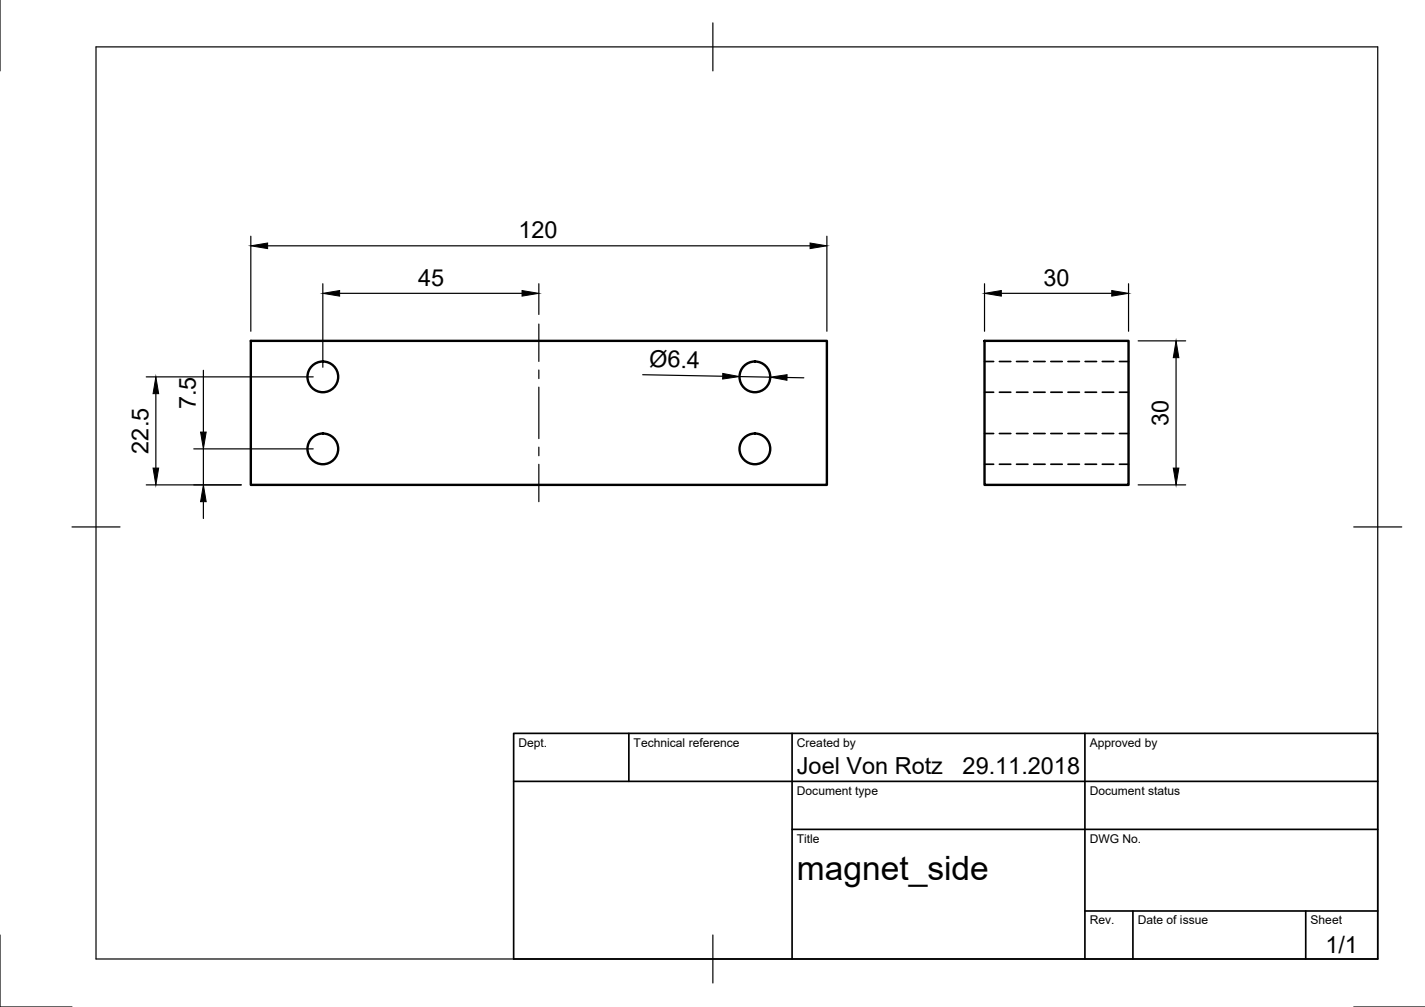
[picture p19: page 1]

Dept. | Technical reference | Created by Joel Von Rotz 29.11.2018 | Approved by

Document type | Document status

Title magnet_side | DWG No.

Rev. | Date of issue | Sheet 1/1

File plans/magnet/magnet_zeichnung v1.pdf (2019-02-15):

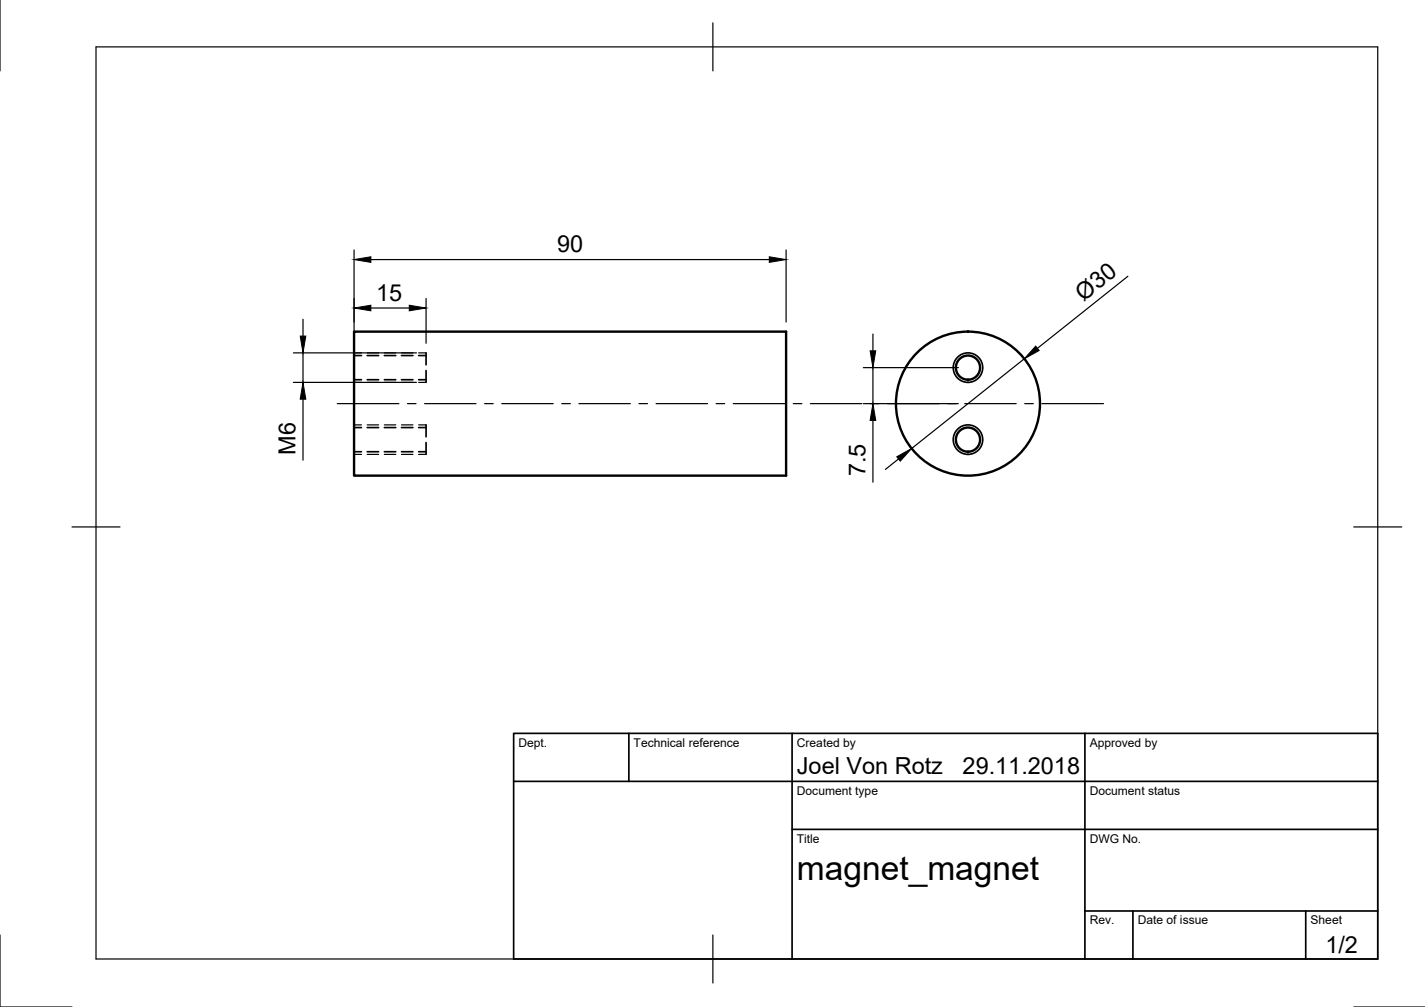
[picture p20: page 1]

Dept. | Technical reference | Created by Joel Von Rotz 29.11.2018 | Approved by

Document type | Document status

Title magnet_magnet | DWG No.

Rev. | Date of issue | Sheet 1/2

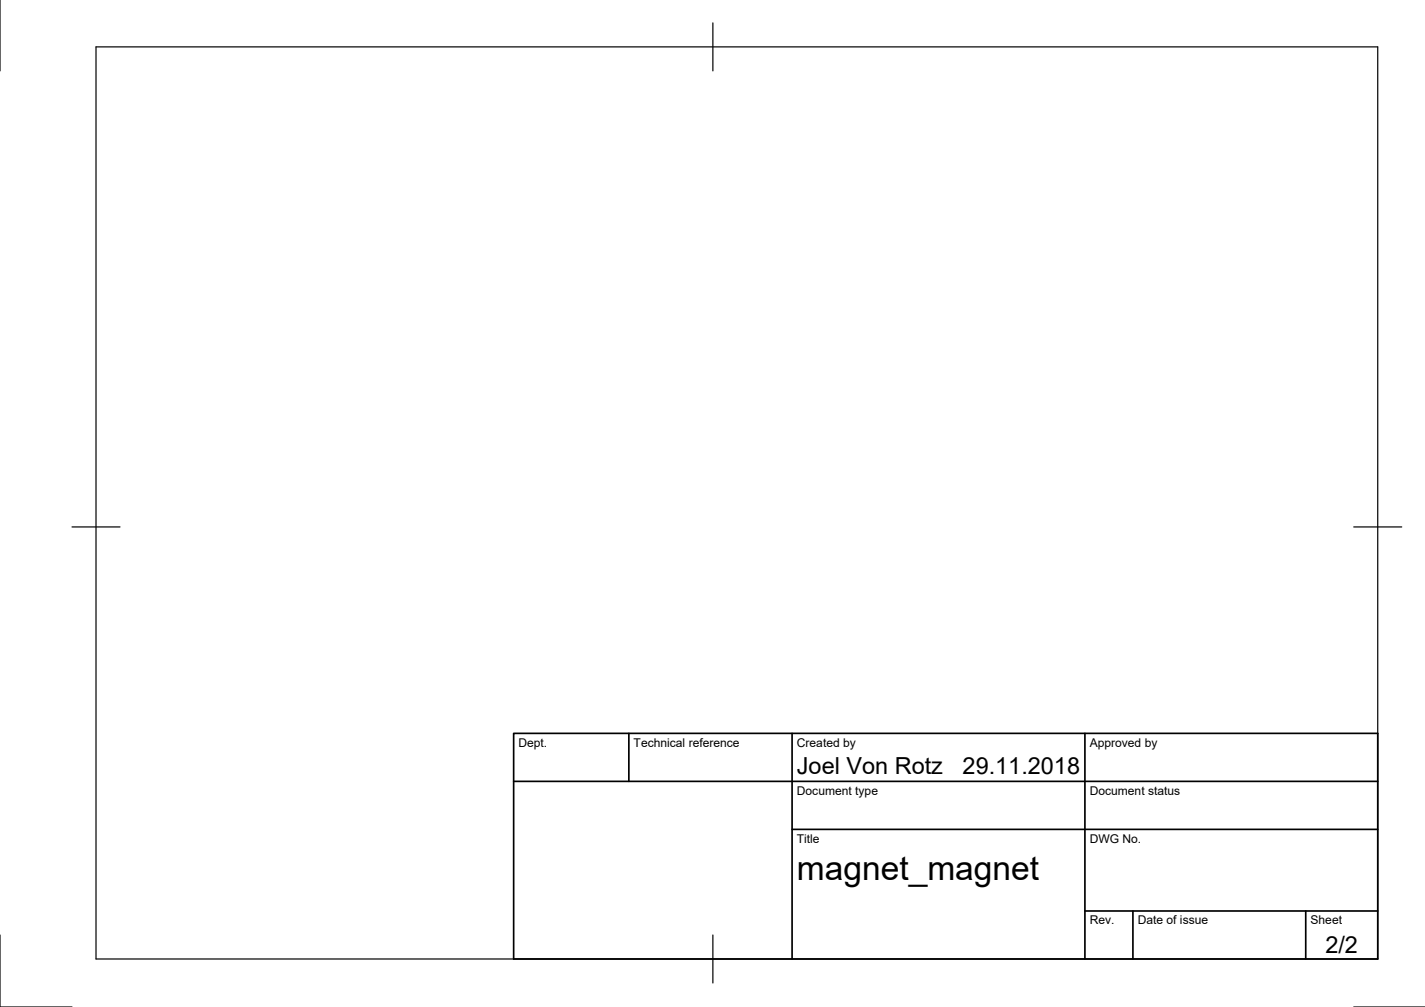
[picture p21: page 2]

Dept. | Technical reference | Created by Joel Von Rotz 29.11.2018 | Approved by

Document type | Document status

Title magnet_magnet | DWG No.

Rev. | Date of issue | Sheet 2/2

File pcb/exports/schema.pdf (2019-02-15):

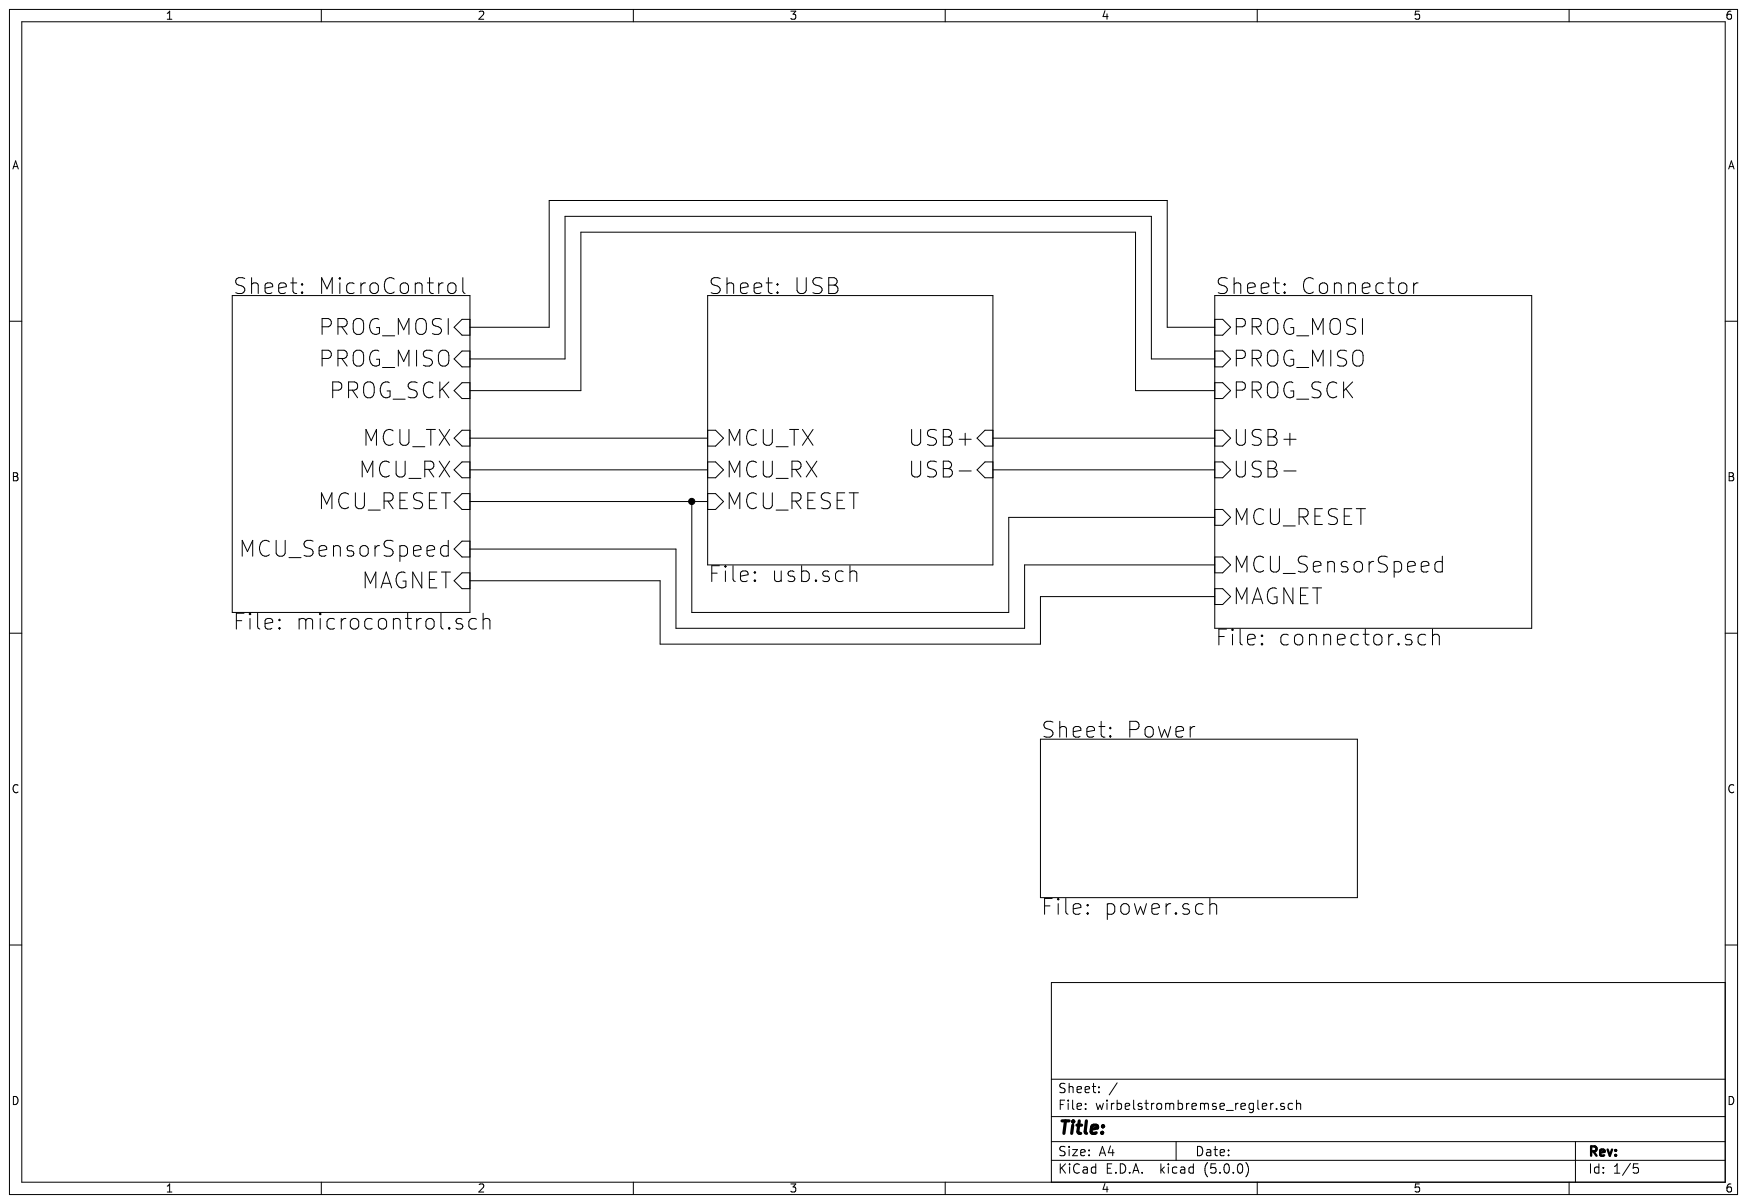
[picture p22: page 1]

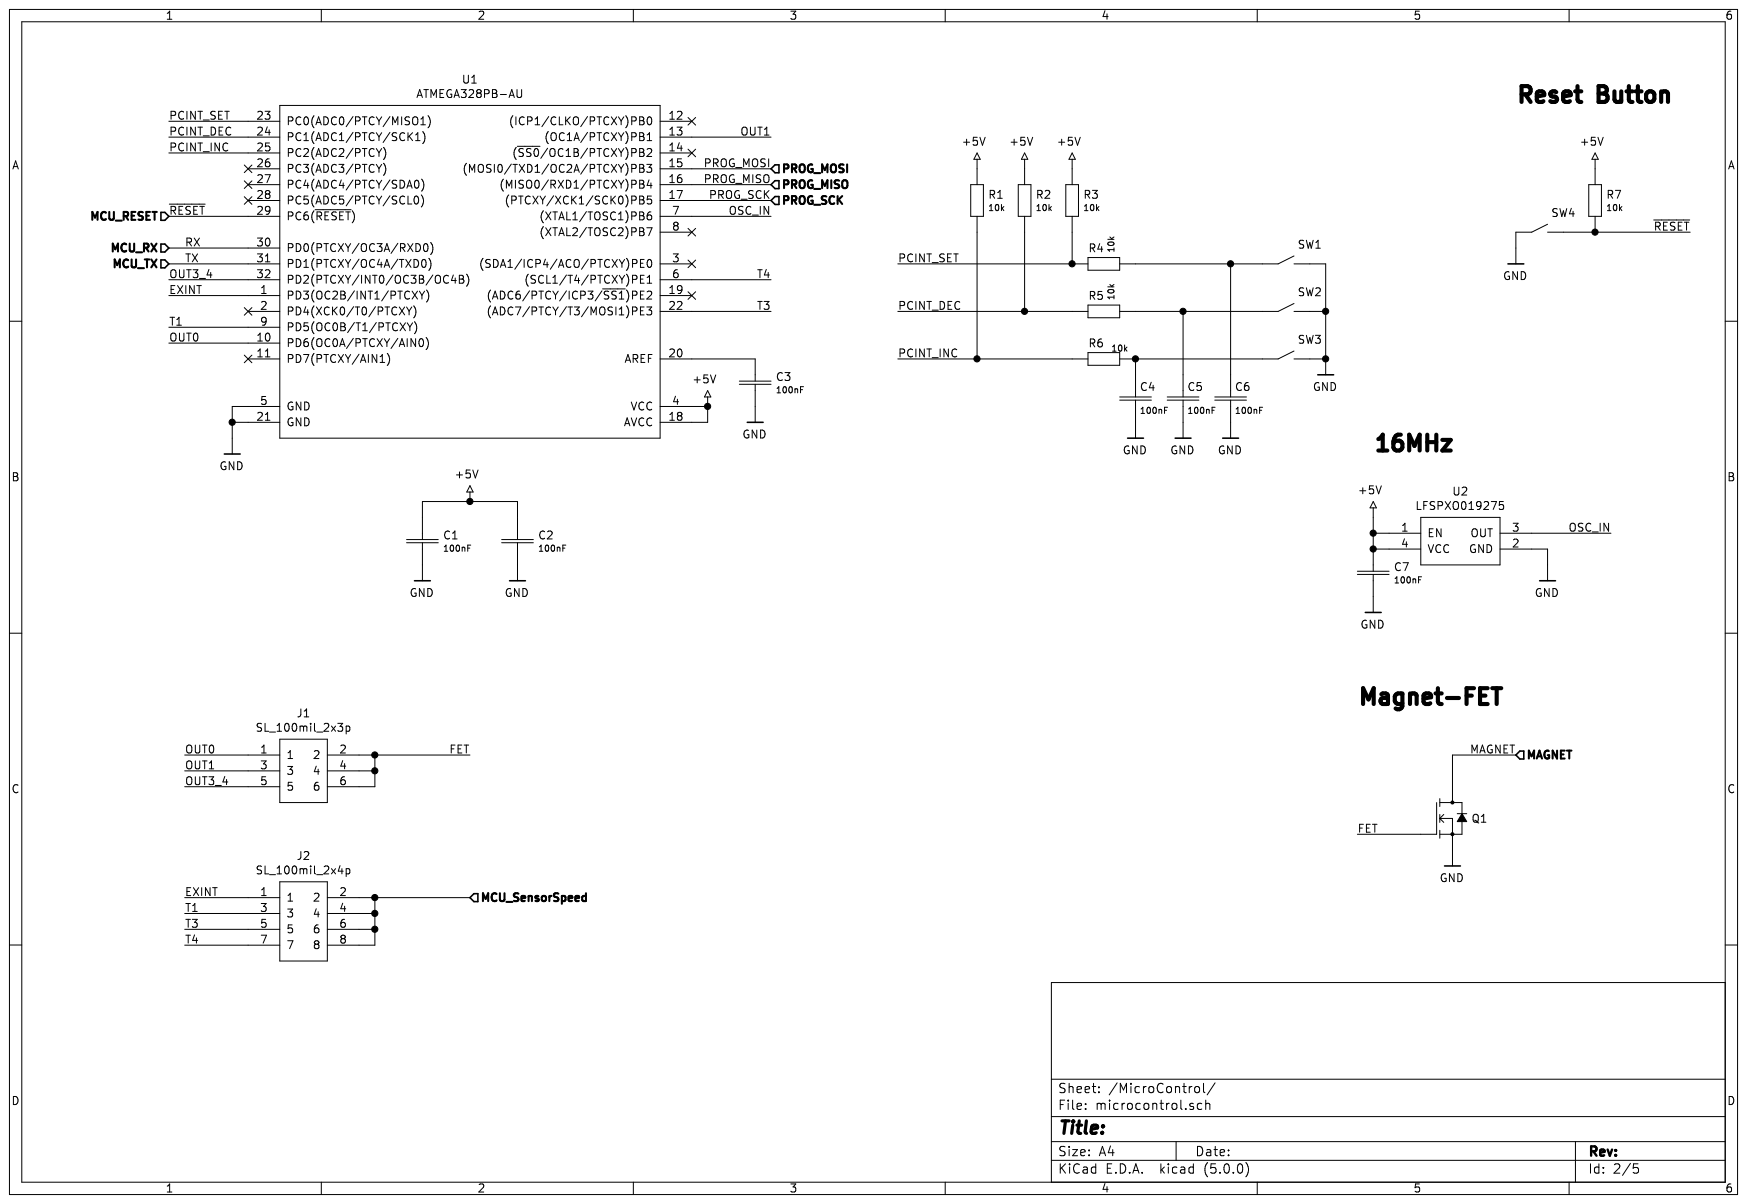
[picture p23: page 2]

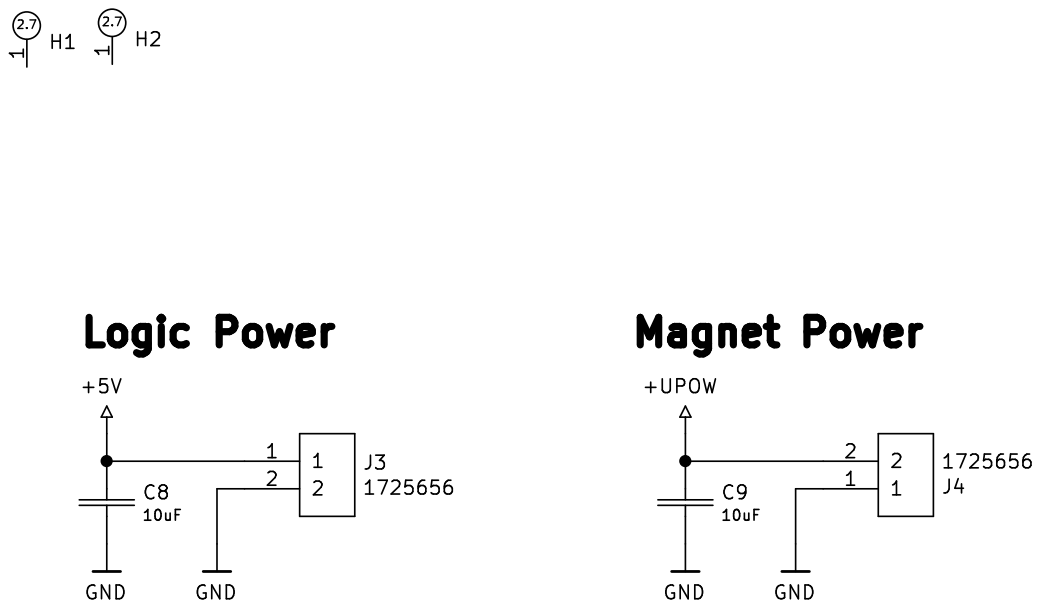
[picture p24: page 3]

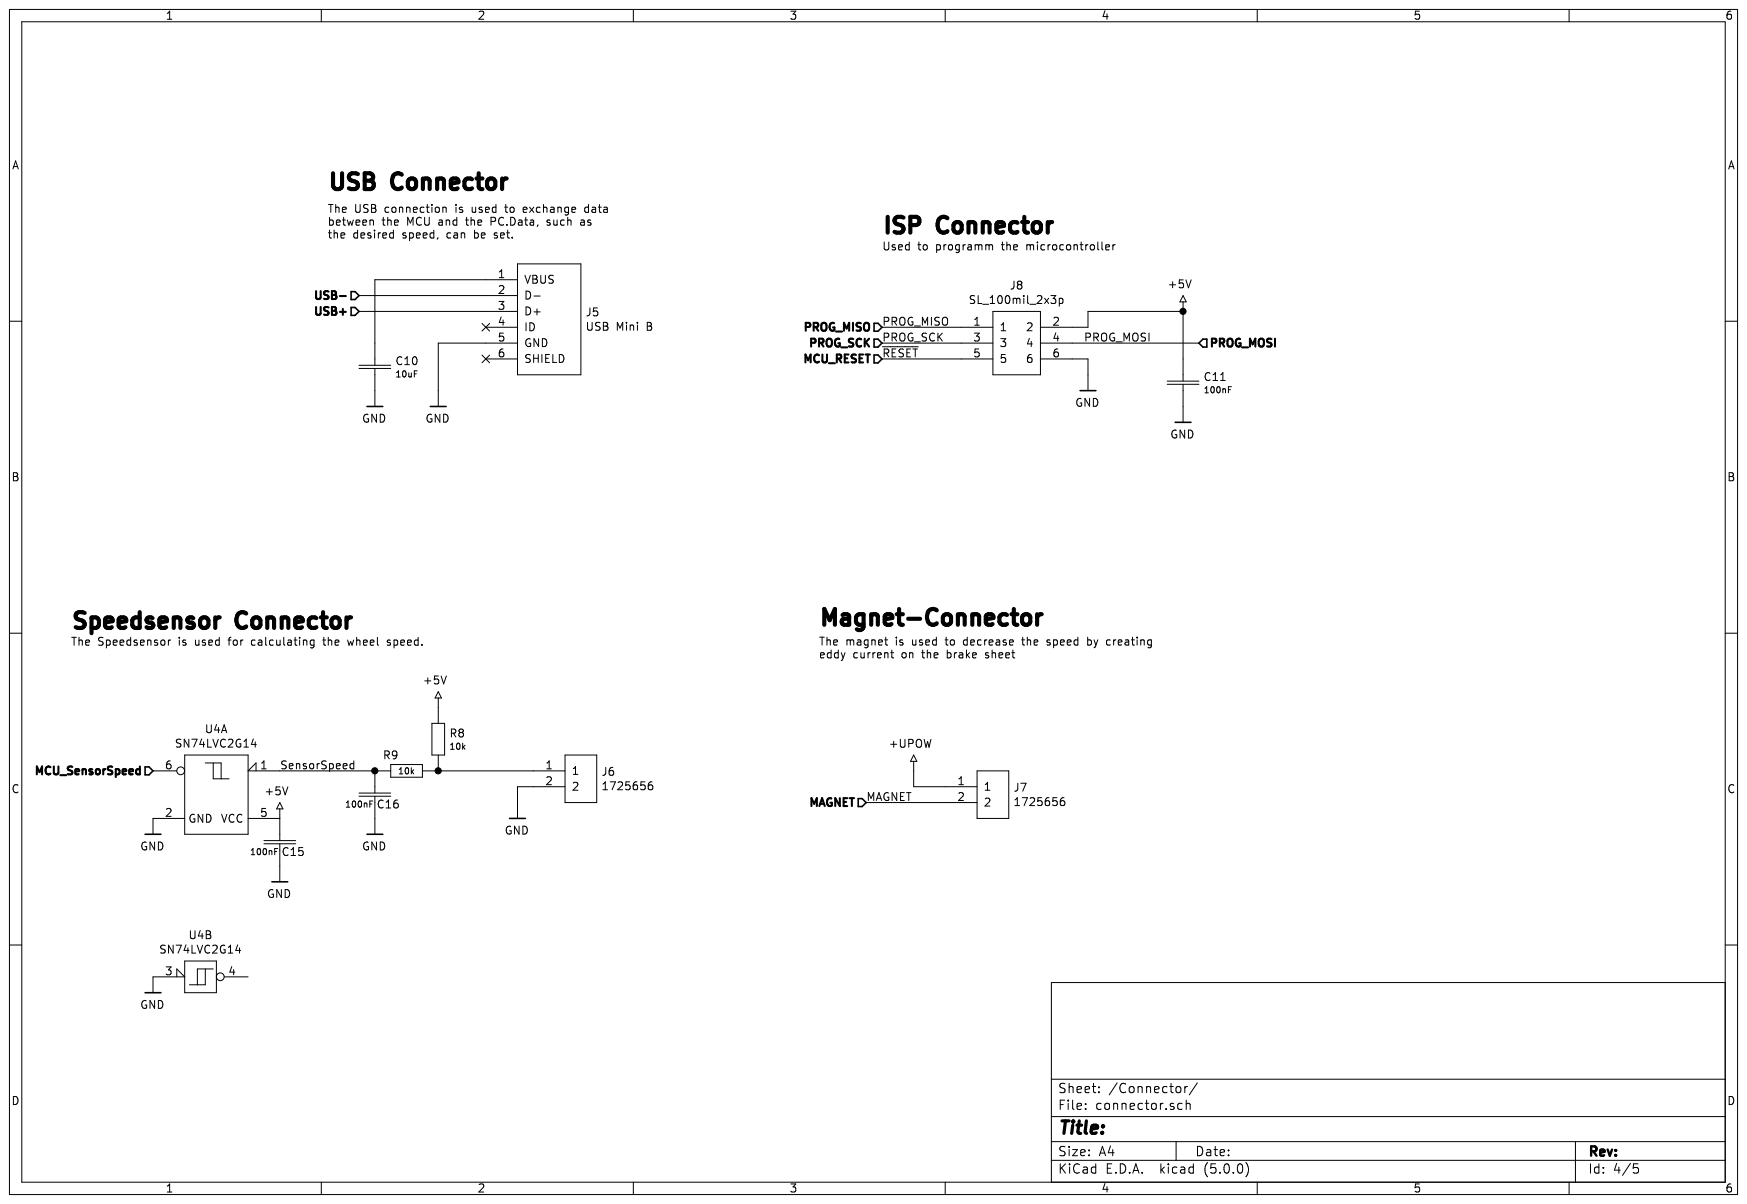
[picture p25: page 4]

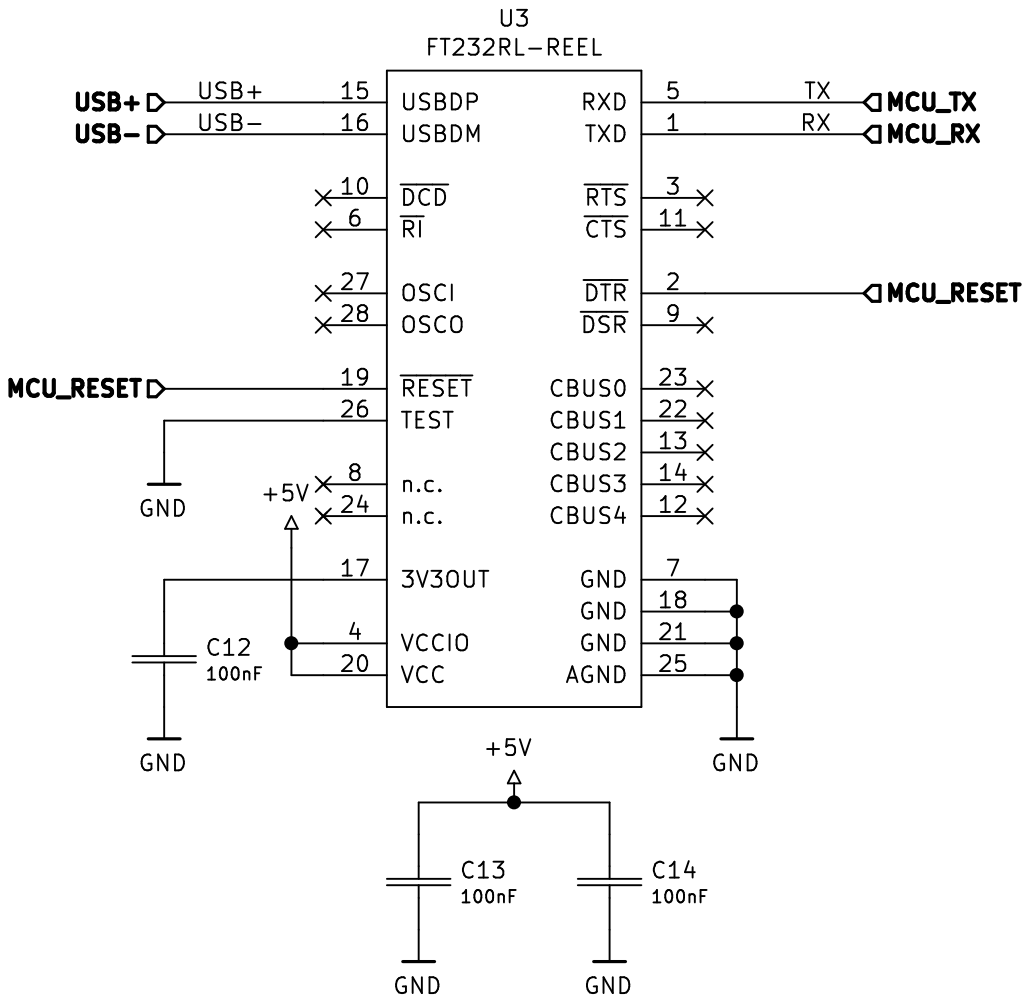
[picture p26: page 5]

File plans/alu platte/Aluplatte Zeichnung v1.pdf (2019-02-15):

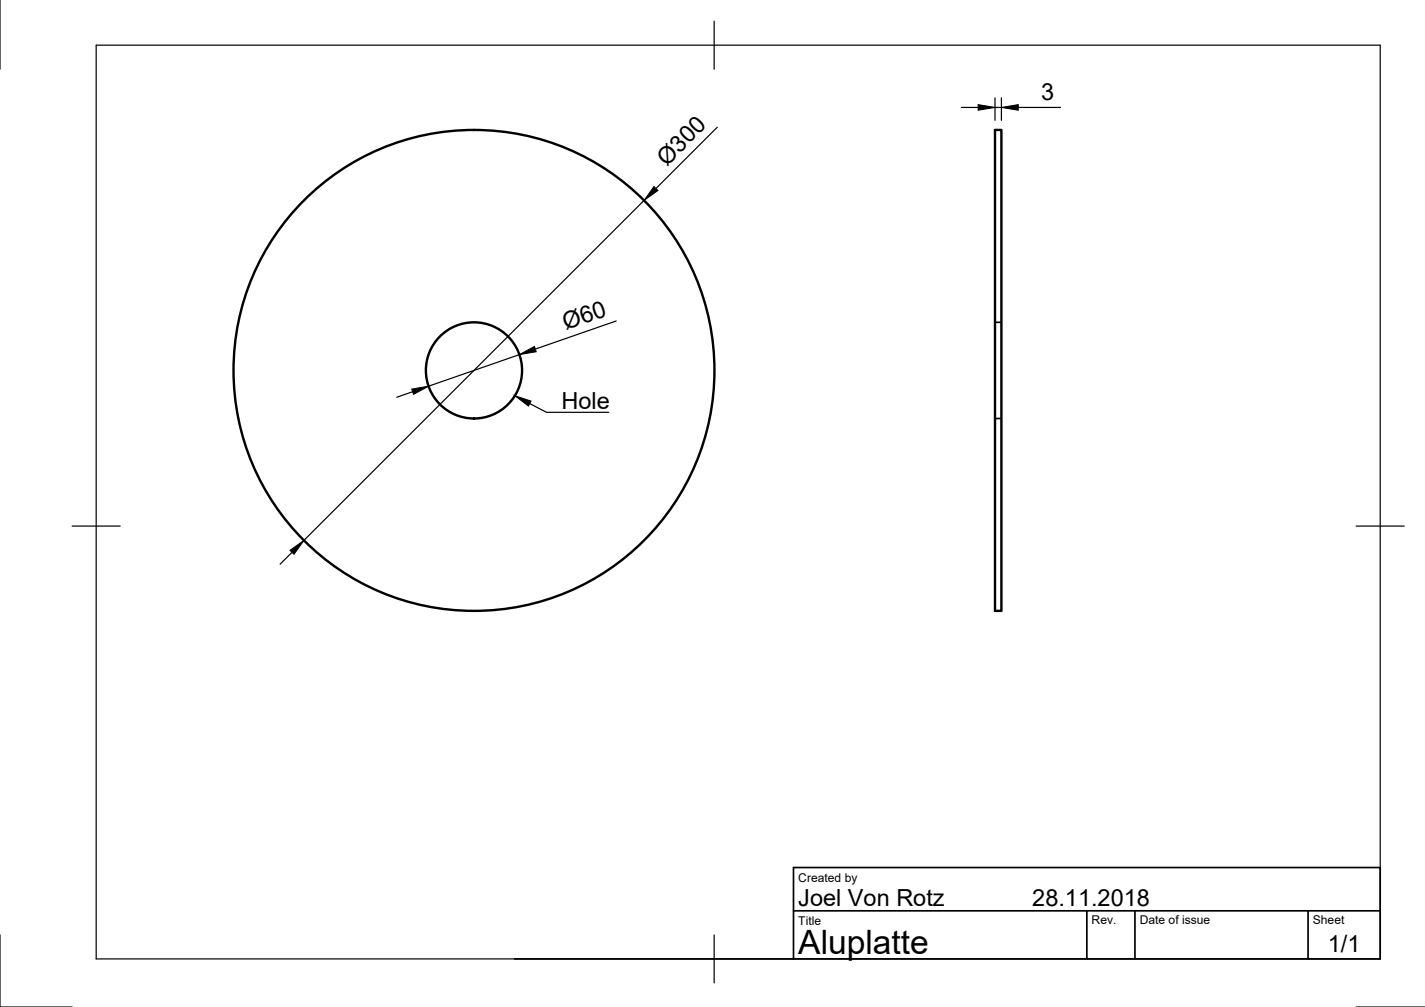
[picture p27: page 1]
Title; Rev.; Date of issue; Sheet

Created by
Joel Von Rotz

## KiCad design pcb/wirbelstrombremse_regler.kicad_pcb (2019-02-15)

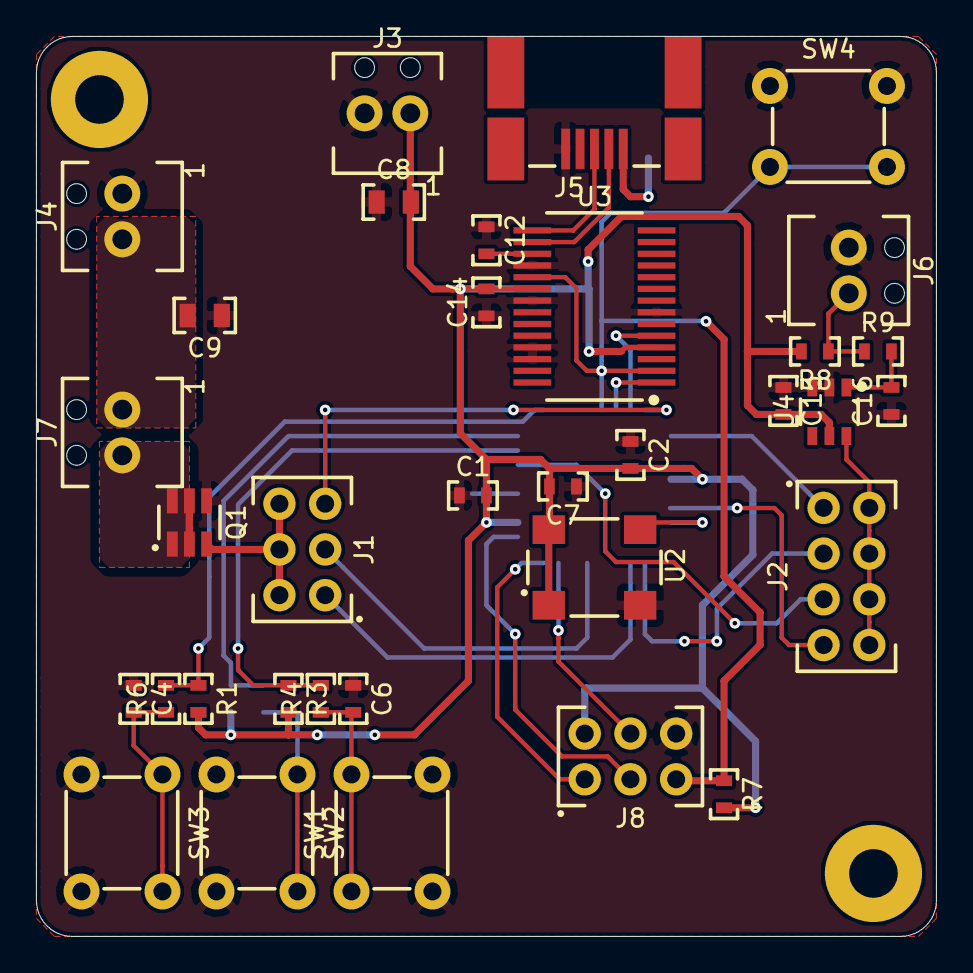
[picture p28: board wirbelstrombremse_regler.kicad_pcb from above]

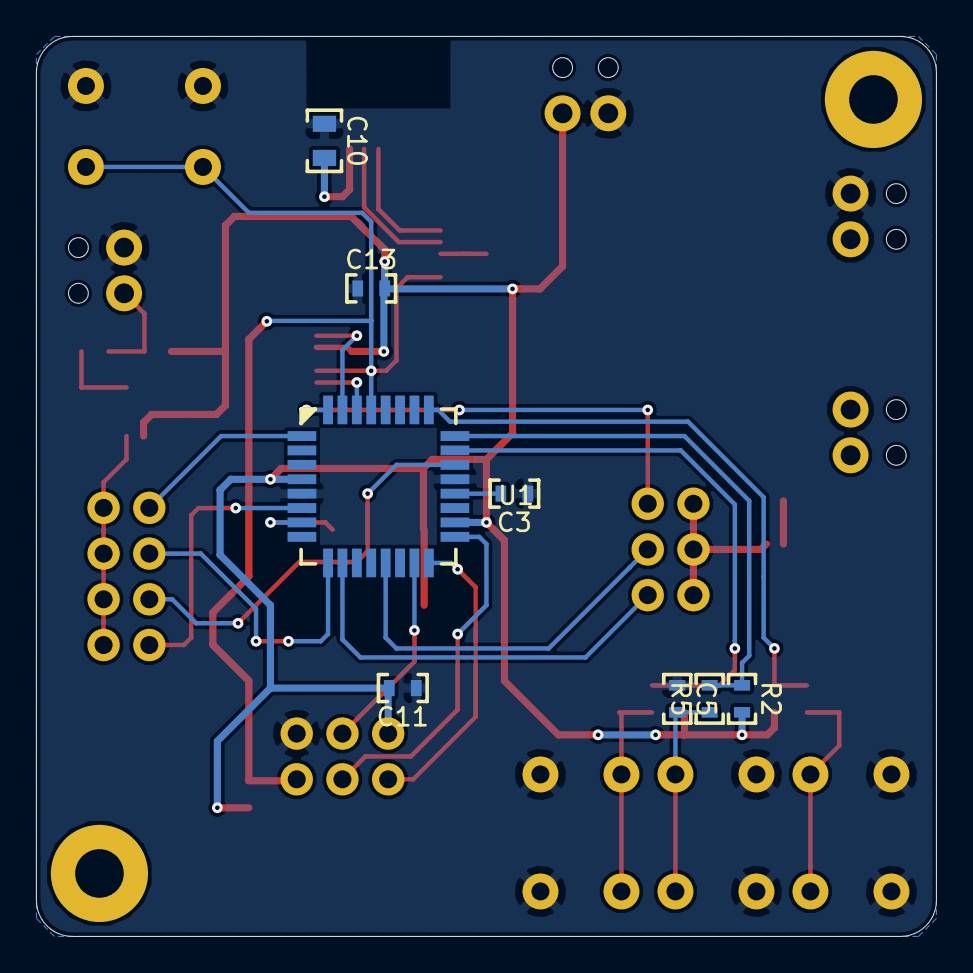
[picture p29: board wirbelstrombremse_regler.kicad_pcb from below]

Board: 2 copper layers, 50.0 x 50.0 mm, 44 parts (8 on the bottom side), 33 nets.

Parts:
C1, C2, C3, C4, C5, C6, C7, C11, C12, C13, C14, C15, C16: CAP_100nF_0603; CAP_0603
C8, C9, C10: CAP_10uF_0805; CAP_0805
H1, H2: HOLE_2.7mm
J1, J8: SL_100mil_2x3p; SL_100MIL_2x3p
J2: SL_100mil_2x4p; SL_100MIL_2x4p
J3, J4, J6, J7: CON_PHOENIX_1725656; CON_MPT_1725656
J5: CON_MOLEX_548190572; MOLEX_54819_0572
Q1: MOSFET_CPH6442; ONSEMI_318BD
R1, R2, R3, R4, R5, R6, R7, R8, R9: RES_10k_0603; RES_0603
SW1, SW2, SW3, SW4: BUT_B3F-1022; BUT_B3F-10XX
U1: ATMEGA328PB-AU; TQFP32_7x7_800
U2: OSZ_LFSPXO019275; IQD_CFPS-72
U3: FT232RL-REEL; SSOP-28
U4: SN74LVC2G14; SOT-23-6

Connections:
+5V: C1.1, C2.1, C7.1, C8.1, C11.1, C13.1, C14.1, C15.1, J3.1, J8.2, R1.1, R2.1, R3.1, R7.1, R8.1, U1.4, U1.18, U2.1, U2.4, U3.4, U3.20, U4.5
+UPOW: C9.1, J4.2, J7.1
/Connector/MAGNET: J7.2, Q1.1, Q1.2, Q1.5, Q1.6
/Connector/MCU_RESET: J8.5, R7.2, SW4.3, SW4.4, U1.29, U3.2, U3.19
/Connector/MCU_SensorSpeed: J2.2, J2.4, J2.6, J2.8, U4.6
/Connector/PROG_MISO: J8.1, U1.16
/Connector/PROG_MOSI: J8.4, U1.15
/Connector/PROG_SCK: J8.3, U1.17
/Connector/SensorSpeed: C16.1, R9.1, U4.1
/Connector/USB+: J5.3, U3.15
/Connector/USB-: J5.2, U3.16
/MicroControl/EXINT: J2.1, U1.1
/MicroControl/FET: J1.2, J1.4, J1.6, Q1.3
/MicroControl/MCU_RX: U1.30, U3.1
/MicroControl/MCU_TX: U1.31, U3.5
/MicroControl/OSC_IN: U1.7, U2.3
/MicroControl/OUT0: J1.1, U1.10
/MicroControl/OUT1: J1.3, U1.13
/MicroControl/OUT3_4: J1.5, U1.32
/MicroControl/PCINT_DEC: R2.2, R5.1, U1.24
/MicroControl/PCINT_INC: R1.2, R6.1, U1.25
/MicroControl/PCINT_SET: R3.2, R4.1, U1.23
/MicroControl/T1: J2.3, U1.9
/MicroControl/T3: J2.5, U1.22
/MicroControl/T4: J2.7, U1.6
GND: C1.2, C2.2, C3.2, C4.2, C5.2, C6.2, C7.2, C8.2, C9.2, C10.2, C11.2, C12.2, C13.2, C14.2, C15.2, C16.2, J3.2, J4.1, J5.5, J6.2, J8.6, Q1.4, SW1.3, SW1.4, SW2.3, SW2.4, SW3.3, SW3.4, SW4.1, SW4.2, U1.5, U1.21, U2.2, U3.7, U3.18, U3.21, U3.25, U3.26, U4.2, U4.3
unnamed: C3.1, U1.20
unnamed: C4.1, R6.2, SW3.1, SW3.2
unnamed: C5.1, R5.2, SW2.1, SW2.2
unnamed: C6.1, R4.2, SW1.1, SW1.2
unnamed: C10.1, J5.1
unnamed: C12.1, U3.17
unnamed: J6.1, R8.2, R9.2

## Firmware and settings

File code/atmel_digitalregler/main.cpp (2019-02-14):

#define F_CPU 16000000UL
#define __AVR_ATmega328PB__
//=================================================================================================
#include <avr/io.h>
#include <avr/interrupt.h>
#include <stdio.h>
#include <stdlib.h>
//=================================================================================================
/* EDDY CURRENT BRAKE
 * This code is written for our vocational matura school project, a regulated eddy current brake.
 * By regulated it's meant to limit the velocity of a wheel to a preset velocity. Using Timers 
 * and Interrupts, the ATMEGA328PB (note the B(ee) as it contains 3 16-Bit timers) can measure
 * speed and put out a PID-regulated PWM. Obviously, this PWM will be controling the magnet, that
 * creates the magnetic field and the eddy current.
 * 
 * For those having the ability to understand the programm, please feel free to suggest any 
 * changes to the code. If everything works out (or if not) I want to continue working on this.
*/
//=================================================================================================
#define TIMER_SPEED_COMPARE_VALUE       1562    //this will result in a interval of ~25ms
#define TIMER_REGULATOR_COMPARE_VALUE   1250    //this will result in a interval of ~20ms
#define TIMER_SPEED_PRESCALER           8       //prescaler of the speed counter (overflow)

#define WHEEL_DIAMETER_m  0.3
#define WHEEL_RADIUS_m    (WHEEL_DIAMETER_m/2)
#define PI                3.1415926535897932384f


#define USB_Readable      (UCSR0A & (1<<RXC0)) //check if data is available in the register DR0
#define PWM_16BIT_TOP     0x0190

#define TIMER_FREQUENCY   0.000016f

#define I                 7       //Bit position of Global Interrupt Enable Bit
//=================================================================================================
/* PID-regulator variables
 * 
 */
const float _Kp   = 0.5f; //proportional factor
const float _Kd   = 0.10f; //derivative factor
const float _Ki   = 0.3f; //integral factor
const float _dt   = 0.02f;        //delta timer (of timer) 20ms
      float error = 0;    //e = w-r -> error = desired - current 
      float Dout    = 0;    
      float Pout    = 0;
      float Iout    = 0;
      float _old_error = 0; //used for derivative term
      float _integral = 0;
const float _max  = 1.0f;
const float _min  = 0.0000000001f; //since comparing floats doesn't really work that well, a very small number can be still used for comparing
      float output = 0;

//=================================================================================================
//Actually those definions don't really interact with the code itself, it's mostly to know which 
//function uses which timer
#define PWM_TIMER         TIMER1
#define REGULATOR_TIMER   TIMER3
#define SPEED_TIMER       TIMER4
#define SPEED_INTERRUPT   TIMER4_CAPTURE
//================================================================================================
#define ENTER_KEY         13

int       time_counter        = 0;
float     speed_time_current  = 0;

float     speed_desired;
float     speed_current;

bool      flag;
uint16_t  usart_index;
char      usart_buffer[32];
char      dummy_buffer[32];
char      result_buffer[32];

// FUNKTIONSPROTOTYP ==============================================================================
bool      init_system(void);
bool      init_regulator(void);
bool      init_speedCalculator(void);
bool      init_usart(uint32_t baudrate);
bool      init_pwm(void);

void      enable_interrupts(void);
void      start_regulator(void);
void      start_speedCalculator(void);
void      start_pwm(float dutycycle);
void      pwm_dutycycle(float dutycycle);

void      usb_transmit(uint8_t data);
void      usb_transmitString(const char* data);
uint8_t   usb_receive(void);
void      usb_handler(void);

// MAIN ===========================================================================================
int main(void)
{
  init_system();
  init_pwm();
  init_regulator();
  init_speedCalculator();
  init_usart(115200);
  enable_interrupts();
  start_speedCalculator();
  start_pwm(0.0f);
  start_regulator();
  while(1)
  {
    usb_handler();
    if(flag)
    {
        flag = 0;
        dtostrf(speed_time_current,8,6,dummy_buffer);    //Atmel doesn't allow for floats to be printed -> dtostrf turns the float into a String based on the set size
        sprintf(result_buffer,"%s\n\r",dummy_buffer); //afterwards the string can be filled with additional commands
        usb_transmitString(result_buffer);        //

        /*doesn't seem to really work, oh well, should look into after documentation has been written*/
        //dtostrf(output,8,6,dummy_buffer);    //Atmel doesn't allow for floats to be printed -> dtostrf turns the float into a String based on the set size
        //sprintf(result_buffer,"%s\n\r",dummy_buffer); //afterwards the string can be filled with additional commands
        //usb_transmitString(result_buffer);        //
        
    }
  }
}

// USB ============================================================================================
/* USB HANDLER
 * The USB handler is used for receiving commands.
 */
void usb_handler(void)
{
    if(USB_Readable)
    {
      usart_buffer[usart_index] = usb_receive();
      if(usart_buffer[usart_index] == NULL || usart_buffer[usart_index] == ENTER_KEY)
      { //indicate that a full message has been sent
        if(usart_buffer[0] == '?' && usart_buffer[1] == 's')
        {
          for(int x = 0 ; x < 30 ; x++)
          {
            usart_buffer[x] = usart_buffer[2+x];
          }
          speed_desired = static_cast<float>(atof(usart_buffer));
          
          dtostrf(speed_desired,5,4,dummy_buffer);    //Atmel doesn't allow for floats to be printed -> dtostrf turns the float into a String based on the set size
          sprintf(usart_buffer,"!s%s\r",dummy_buffer); //afterwards the string can be filled with additional commands
          usb_transmitString(usart_buffer);        //
          
        }
        usart_index = 0;
      }
      else
      {
        usart_index++;
      }
    }
}

void usb_transmit(uint8_t data)
{
  while (!( UCSR0A & (1 << UDRE0))); // wait while register is free
  UDR0 = data; // load data in the register
}

void usb_transmitString(const char* data)
{
  uint16_t index = 0;
  while(data[index] != '\0') //stop sending when null (End of Message) has been reached
  {
    while (!(UCSR0A & (1 << UDRE0))); // wait while register is free
    UDR0 = data[index]; // load data in the register
    index++;
  }
}

uint8_t usb_receive(void)
{
  return UDR0;
}

// INITIALIZATION =================================================================================
bool init_system(void)
{
  usart_index        = 0;
  time_counter       = 0.0;
  speed_time_current = 0;
}

bool init_pwm(void)
{
  DDRB   |= (1 << DDRB1); //set timer-output as an output

  TCCR1A |= (1 << COM1A1); //map PWM-output to OC1A as non-inverting -> PWM-mode
  TCCR1A |= (1 << WGM11);  //configure timer 1 to Fast-PWM 16-Bit
  TCCR1B |= (1 << WGM12) | (1 << WGM13); // ^^^
  ICR1    = PWM_16BIT_TOP; //When timer reaches this value, the timer resets
  OCR1A   = 0x00; //set duty cycle to 0% / Small spikes happen, which is noted in the datasheet
}

bool init_speedCalculator(void)
{
  TCCR4B |= (1 << WGM42);
  TIMSK4 |= (1 << OCIE4A) | (1 << ICIE4);
  TCNT4   = 0x0000;
  OCR4A   = TIMER_SPEED_COMPARE_VALUE - 1;
}

bool init_regulator(void)
{
  TCCR3B |= (1 << WGM32);
  TIMSK3 |= (1 << OCIE3A);
  TCNT3   = 0x0000;
  OCR3A   = TIMER_REGULATOR_COMPARE_VALUE - 1;
}

bool init_usart(uint32_t baudrate)
{
  static uint16_t baud;
  
  if(baudrate == 115200)
  {
    baud = 8;
  }
  else
  {
    //formula to calculate baudrate register value for the MCU
    baud = static_cast<uint16_t>((F_CPU/(16 * baudrate)) - 1);
  }
  UBRR0L  = baud & 0xFF;
  UBRR0H  = (baud >> 8) & 0xFF;
  UCSR0C |= (1 << UCSZ00) | (1 << UCSZ01);  //8-bit mode
  
  UCSR0B |= (1<<TXEN0) | (1<<RXEN0);        //enable Transmitter and Receiver
}

// START ==========================================================================================
/* START TIMER
 * By setting a prescaler, the timer for the regulator and for the speed calculator are activated
 */
void start_regulator(void)
{
  TCCR3B |= (1 << CS32);
}
void start_speedCalculator(void)
{
  TCCR4B |= (1 << CS42);
}

/* START PWM
 * As the name of the function says, it enables the PWM and sets the duty cycle.
 * This function is separate from the initialization function to achieve a better code-structure.
 */
void start_pwm(float dutycycle)
{
  OCR0A   = static_cast<uint16_t>(PWM_16BIT_TOP * dutycycle);
  TCCR0B |= (1 << CS00); //set prescaler to 1 / start timer
}

// OTHER FUNCTIONS ================================================================================
/* ENABLE INTERRUPTS
 * This enables the use of the interrupts -> Timer Capture Interrupt, Timer Interrupt
 */
void enable_interrupts(void)
{
  SREG |= (1 << I);
}

/* PWM SET DUTYCYCLE
 * 
 */
void pwm_dutycycle(float dutycycle)
{
  OCR0A   = static_cast<uint16_t>(PWM_16BIT_TOP * dutycycle);
}

// ISR ============================================================================================
/* SPEED CAPTURE
 * The capture feature is used to get the speed of the wheel. By adding the timer value and
 * the overflow times (below) the total amount of time from one impulse to the next
 * impulse can be calculated.
 */
ISR(TIMER4_CAPT_vect)
{
  TCNT4 = 0;
  speed_time_current = (time_counter * 0.024992f + TIMER_FREQUENCY * static_cast<float>(ICR4));
  speed_current      = (0.15*2*PI/speed_time_current);
  time_counter       = 0;
  flag  = 1;
}
/* SPEED OVERFLOW
 * When there is no impulse for the speed time, a overflow occurs (not a real one, but just a counter, 
 * indicating a specific time has passed, which can be added together at the end).
 */
ISR(TIMER4_COMPA_vect)
{
  time_counter++;
}

/* REGULATOR COMPARE (PID Regulator)
 * 
 */
ISR(TIMER3_COMPA_vect)
{
  error = speed_current - speed_desired;

  Pout = _Kp * error;

  _integral += error * _dt;
  Iout = _Ki * _integral;

  float _derivative = (error - _old_error) / _dt;
  Dout = _Kd * _derivative;

  output = Pout + Dout + Iout;

  if(output > _max)
  {
    pwm_dutycycle(1.0f);
  }
  else if(output < _min)
  {
    pwm_dutycycle(0.0f);
  }
  else
  {
    pwm_dutycycle(output);
  }

  _old_error = error;
}
//=================================================================================================

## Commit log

2019-02-14 added attachment files
2019-02-14 added more files
    [d_regler_nf.csv, i_regler_nf.csv, mit_mag_mit_rad.csv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]
2019-02-15 added pcb and plans
    [connector.sch, microcontrol.sch, power.sch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]
